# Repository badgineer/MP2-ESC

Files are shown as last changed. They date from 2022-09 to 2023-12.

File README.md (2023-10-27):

# **MP2_ESC** 
Multi-Platform, Modular, Powerful Electronic Speed Control

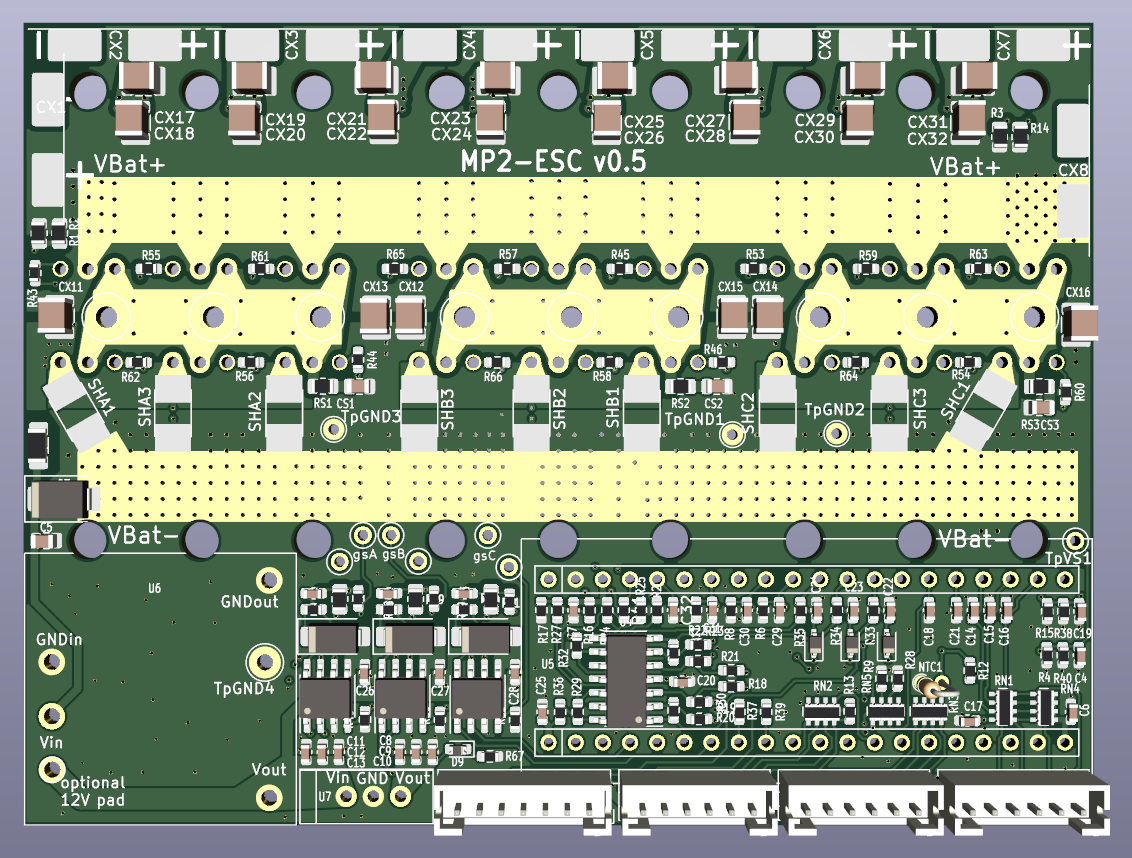
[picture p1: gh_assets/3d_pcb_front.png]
3D_PCB


## Design Goals
**Decent power** (18 FET, so 100-300A should be possible depeding of FET choice, Bus Bars, and cooling) \
**Relatively compact design**, fitting for ebikes / medium-large electric scooters, and cheap to order \
**Modular**, with easily replaceable modules (both bluepill and blackpill compatible hardware wise, 12V and 5V DC-DC stages are modules also) \
**Standard footprint parts**, so replacement parts can be found easily in case of original parts out of stock or out of production \
**Optimized for low cost** production by JLCPCB, including SMT assembly.  \
**Possibility to buy the SMD parts pre-soldered:** All SMDs are on the same side, in large stock at lcsc (at the time of writing), so the board can be ordered with SMDs pre-assembled by JLCPCB for a decent price. \
**To our knowledge, important feature that is not available on most open source ESCs:**
* hardware overcurrent proection (triggers at 430A)

## Compatibility with variaty of Open-Source VESC projects
VESC with [ STM32F405 pill ](https://github.com/davidmolony/F405_pill)  \
VESC with GD32F303CG pill (Netzpfuscher mod, note CG) \
EBICS with F103 Bluepill (Stancecoke) \
[SmartESC V3 (Casainho)](https://github.com/casainho/SmartESC_STM32_v3) \
[SmartESC V2 (Netzpfuscher/Koxx3)](https://github.com/Koxx3/SmartESC_STM32_v2) \
MESC with F401 Blackpill (MxlemmingFOC) \
STM32 Motor Control Workbench (F401, F103)

## PCB
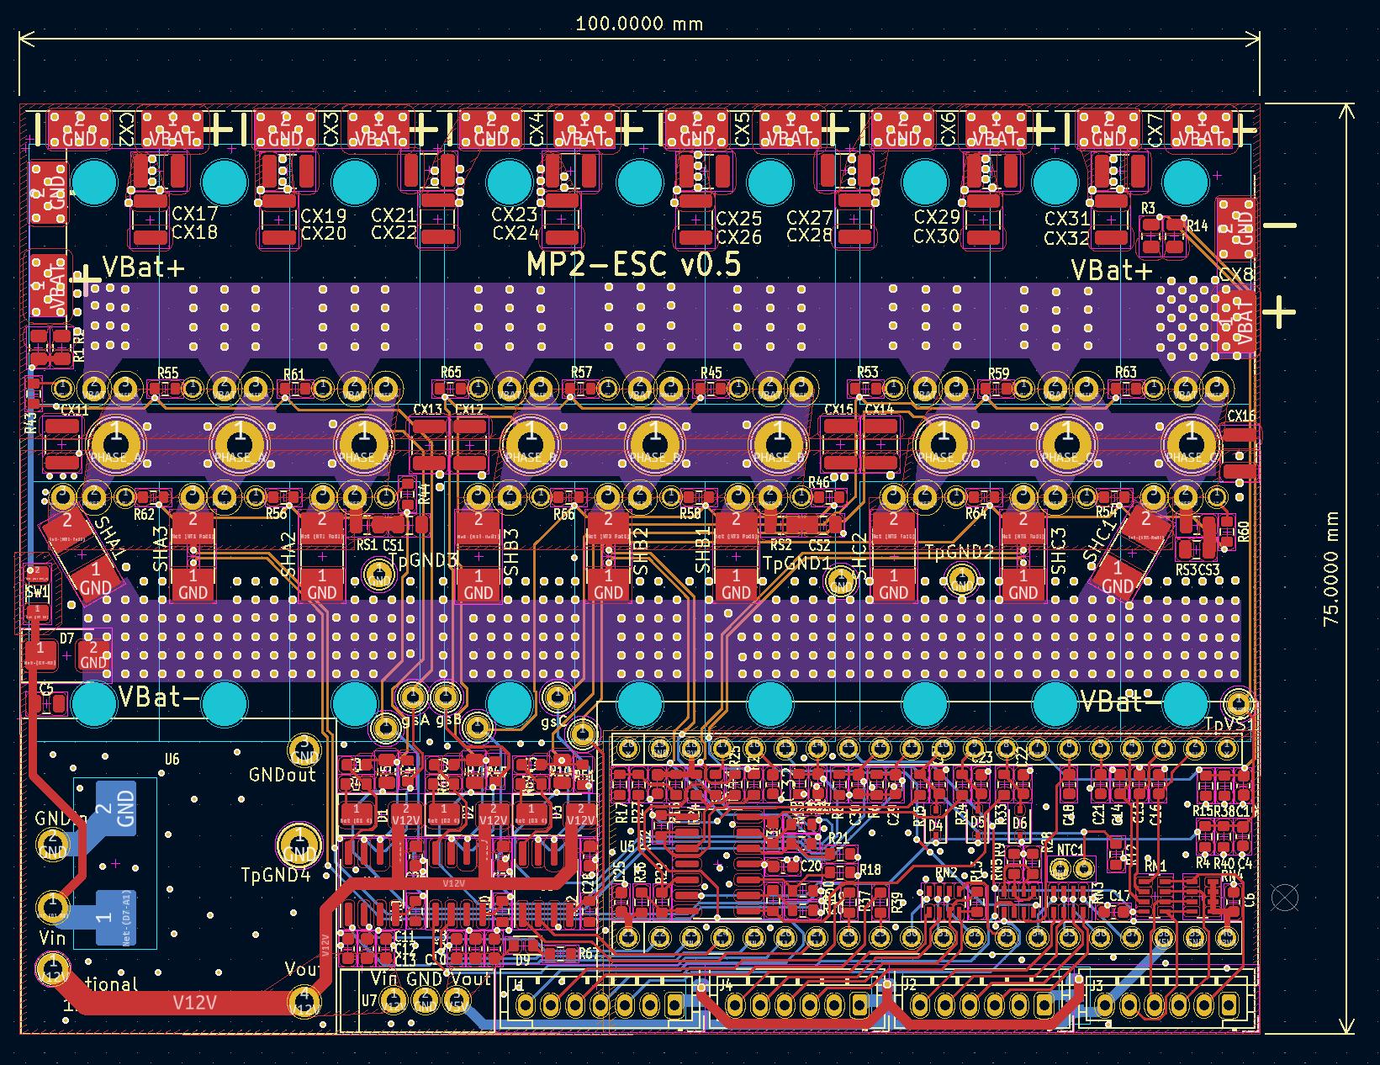
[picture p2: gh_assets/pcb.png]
PCB


## Required software
The circuit design tool used for this project: [KiCad](https://www.kicad.org/).

## Endless Sphere Thread:
https://endless-sphere.com/forums/viewtopic.php?t=117045

## Safety
The high amperage and compact design of this board means that it is inherently prone to arcing. For this reason we urge you to engage in the following safety precautions:

* Remove all sources of power when operating on the board. This includes soldering, mounting the board, connecting wires, or plugging in the pill
* Use an [USB isolator](https://www.amazon.com/s?k=usb+isolator) when connecting to your computer
* **DO NOT USE LIPO BATTERIES INDOORS**
* The board stores considerable capacitance -- a spark when you connect to your power supply
* Ideally you should use a current limited power supply when testing
* Before powering up **follow all recommendations in our building tips section**.

## Building Tips

Soldering, assembly, safety and testing are [here](docs/PCB_ASSEMBLY_TESTING.md).

### **Bus Bars**
Bus bars are recommended for anything else than very low current. (extra copper wires/bars/plates soldered to the exposed copper strips of the PCB, or at very least a ton of solder on the exposed strips, but this last variant only for low phase currents). See [this document](docs/HIGHER_AMP_ASSEMBLY.md) for examples. 

### **Bulk electrolytic capacitors (XC.... )**
We recommend a total of 2000uF for low phase currents (up to ~150A) and 3000uF or more for high battery currents. There are 2 smt pads at the ends of the Vbat bus bar, and another 6 on the top for usecases where a lot of capacitance is needed.
General considerations: You need more capacitance the more phase current you plan to use, and the longer (and thinner) your battery wires are. So you can probably also get away with less if you have short thick battery wires.  

Choose voltage rating ~ 1.5x your max battery voltage for a long lifetime. For 48v nominal (54.6V max) battery voltage, 80V or more is recommended. Or just use the same rating as your FETs.  
The total capacitance of the electrolytic capacitors is more important than the exact combination of values. More smaller capacitors probably have a slight advantage over fewer large ones: lower ESR, lower parasitic inductance, and redundancy in case of failures.

### **Bulk ceramic/MLC capacitors:  (XC.... )**
As much as possible. These need to compensate for the high frequency weakness of the electrolytic capacitors. Overrating voltage rating is recommended. 

### **Capacitors - the rest**
Values are consolidated for easy buying. Voltage rating is 25V or higher regardless if they are on the 12v, 5v, or 3v3 rail on the default design, however you can choose a smaller voltage rating for the 5v and 3v3 rails..  

### **Snubbers (RSx, CSx)**
These are RC snubbers. **They are here only for the footprints. Do not fit them (yet).** The real values (if necessary at all) will be computed after we build the controller and see what ringing we get. Purpose of the snubbers is to dampen that ringing. (if you choose different parts than the one we compute the snubbers for, you might need to compute the snubbers yourself). These components are not present in the pick-and-place or BOM files.

### **MOSFETs**
The default MOSFETs are available from lcsc at the time of writing. They are cheap and have good specs. (low Rds on, low Crss, 100v, etc). 
You can use a FET of your choosing, but please be aware that old FETS (such as the famous 4110 or 3077) have huge Crss, leading to a tiny Ciss/Crss ratio. This ratio needs to be bigger than roughly your max battery voltage, so you will need to compute and add the optional Cgs capacitors (OCx). Small Ciss/Crss results in ringing / parastic turn on (which leads to failure). 
That being said, it’s best to just use FETs with Ciss/Crss > ~100, nowadays they’re easy to find. See the section with alternative parts below.

Some additional material on MOSFET selection and testing is [here](docs/MOSFET_PARAMETERS.md).

Attach the FETs to a heatsink: the FETs need to be electrically isolated from the heatsink, but well connected thermally. The options for this are:
* Mica glass (“traditional option”, cheap, easy to find)
* Ceramics (saw this as a new option, never tried it)
* Polymer pads 
* Kapton Tape 

Unfortunately in focusing on making the board small we crammed the FETs very close together. This means some mica or ceramic pads will not fit - and it’s very hard to cut them afaik. So for this version we’re probably stuck with polymer / kapton. 

### **Board Testing**

* V0.1 build has been tested by mxlemming with MESC FOC firmware on F401CC black pill board, and by Netzpfuscher with his VESC port, in lab conditions. 
* V0.3 has been tested, and reached 280Phase amps on a Surron, with maximum power draw 10kW. There were no overheating problems (though cooling was good, and it was winter). Over 280 Phase amps there were random BRK errors (a fix is being tested)

### **Known issues/limitations:**
* Pills have very few ADCs, so some sacrifices have been made (choice between analog brake and Motor Temp). 
* Gate drivers are not as popular and readily available on lcsc as the other SMD parts
* Having the MCU on a separate board (the "pill" development boards) is a questionable idea from PCB design point of view. In our testing it seemed to work, but we know it's not without drawbacks (main one being pill pins "catch" noise).

## Alternative parts.

### **MOSFETs**
100V: 
* CRST030N10N - Default, cheap, tested, available at lcsc.
* MDP10N027 - Cheap, tested, available on aliexpress.
* IPP023N10N5 - Good, more expensive, not tested.

80V: 
* CRST030N10N - Very cheap, not tested, lcsc.
* IPP019N08NF2S - Good, more expensive, not tested
* IPP016N08NF2S - Very good, more expensive, not tested

150V:
* CRST073N15N
* NCEP15T14
* NTP5D0N15MC - best of the 3 listed here, not tested. 

Generally: There are a lot of TO220 fets to choose from (probably the only real advantage of TO220). If you want another, make sure it has low RDSon, gate charge ~ 160nC, low Crss (Ciss/Crss > Vbat).  

### **Gate Drivers**
* L6498DTR - ST micro. default. not tested yet
* EG2181D - EG micro. not tested, cheap on lcsc
* TF2190M-TAH (TFSS) (LCSC PN: C2917161) -> tested. probably has problems with ulvo, which result in shoot through. not recommended anymore (used to be the default.)
* NCP5183/NCV5183 (On Semi)
* FAN7390 (Fairchild)
* FAN7191 (Fairchild)
* DGD2190M (Diodes Inc)
or any other "replica" of IR2181

### **Operational Amplifier**
* NCS20034 (On Semi) - tested
* GS8634-SR (Gainsil)
* COS724SR (Cosine) - tested. current default recomendation due to specs and LCSC stock
* TSV914 (ST)
* TLV9054 (TI)

### **Pills**
* F405 Pill - [ LINK ](https://github.com/davidmolony/F405_pill) 
* Black Pill
* Blue Pill

### **12V DCDC**
* We recommend isolated:
  * PQDE6W-Q110-S12-D preferred (CUI devices)
  * RD5-110S12W (Rui Da Kang)
  * HLK-10D11012 (HiLink)
  * RDE20110S12 (XP Power)
  * THN 10-7212WIR (TRACO Power)
* Less desireable: unisolated
  * P7805-500 (CUI)
  * Or wire on some [random cheap stuff](https://www.aliexpress.com/item/1005001599313771.html)

### **5V DCDC**
* Tons of options in "TO220 Replacement" format - like [ this random example ](https://www.aliexpress.com/item/1005004807082011.html)
* VXO7805-500 (CUI)
* VX7805-500
* 7805SR-C (Murata)

### **Diodes for "over" protection**
1N5819WS - These are ubiquitous, but it is important you use these due to very low forward voltage. Using anything else will probably result in hardware overcurrent not working.

### **Diodes for bootstrap**
We recently changed from XX4007 in SOD123 package to higher speed diode (US1M). Anything with 100V+ or 150V+ will work... but generally many 1kV diodes are available in common packages, so use them. High speed are preferable, but really most diodes will work...

## Supporting materials
* Gathering motor parameters [[LINK](docs/MOTOR_PARAM.md)]
* MOSFET selection [[LINK](docs/MOSFET_PARAMETERS.md)]
* Pin mappings between MP2 and the F405 pill [[LINK](docs/MP2_F405PILL_PINOUTS.md)]
* MP2 assembly, testing and firmware [[LINK](docs/PCB_ASSEMBLY_TESTING.md)]
* MP2 bus bar methods [[LINK](docs/HIGHER_AMP_ASSEMBLY.md)]
* MESC Firmware on the MP2 -- getting started with STM32CubeIDE [[LINK](docs/FIRMWARE_INTRO.md)]
* Some (bad) examples of connecting the MP2 to a motor [[LINK](docs/QS165_MP2_WIRING.md)]

## Change Log / Known Problems 

### v0.6 change log
* R17 of the opamp comparator changed to 22k -> back to actual 430A overcurrent protection, was 375 out of an error
* removed vsense 2 - hardware overvoltage also limits battery choice, and is of limited usefulness
* changed default bom to accomodate 32s max battery without modifications. See most below changes. 
* changed all ceramic caps on vbat to 250v rated ones
* removed TVS diodes - they only work for a very low voltage interval, so without its more generic
* changed vbat divider network so it's exaclty the same ratio as phase vsense to make it easy to set up the software (just set 150 and 3.3 everywhere) 

### v0.5 change log
* added bootstrap resistors to limit current spikes
* reduced gate pulldowns to 10k for faster fet turnoff in some cases
* changed the default gate driver (old one was suspected of bad behaviour)
* 1 gate resistor per fet now.

### V0.4 known problems
* bluepill is mostly supported - but due to a pinout bug does not have a cap on RST. Take care if you use bluepill! 
* v0.4 not tested at this time. if you do test it, please let us know. 
  
### V0.4 change log. 
* remove vbat solder jumpers. for 150v the board requires a different BOM anyway.
* remove pill solder jumpers. (bluepill compatibility is a bit complicated because of a pinout mistake)
* make overlimit opamp output LPF better suited to an additional LPF on the pill and reducing pin noise. (cap -> 10uF, move it near pin, decrease R value)
* make power switch footprint more accessible, and less arc prone. (bigger, better location)
* move the protective R pair near vbat ("before" the switch)
* increase margins for Vbat and Phase copper areas to reduce short / arc risk
* replace the 4pin JST with a 7pin one and route more of the pill pins to JSTs
* standardize JST pin layout (GND and Vaux are all over the place.)
* add a power led on 5v rai
* added lpf caps on ADC throttle/brake inputs
* made 12v surface routed 
* phase wire pads are now at equal distance from eachother
* adapted to newest F405 pill pinout 
* moved to kicad 7

### V0.3 change log
* reduced shunt value to 0.5mR (from 1mR) for lower heat generation
* increased opamp gain to ~22 (from 10) for compensating lower shunt value
* added solder jumpers for configuring power stage vsense
* faster/better bootstrap diodes for better behavior and lower Qrr loss/heat
* many other tiny changes / improvements

## FAQ

* **What’s with the many solder jumpers?**
Except for the hall sensor JST, all others have a solder jumper for connecting its power pin to 3v3 or 5v, depending on your needs. 

* **Why do the electrolytic caps have surface pads instead of through hole?**
Through hole pads imply a lead through the hole, sticking out on the other side. This would prevent the FETs from sitting flush against the PCB.

* **Can you assemble it for me?**
There is no plan on selling any assembled PCBs. You can get the SMD side pre-assembled at [jlcpcb](https://jlcpcb.com/) (at the time of design all parts were in stock for jlcpcb SMT service). So you’ll only need to solder the through-hole parts and the modules. 

* **I want more power!!!**
This might not go well. So good luck, you’ll probably need it. Please don't blame us when it goes up in smoke. But do let us know how it goes. Disclamer aside, here are some basic suggestions:
   * Review what [other people](docs/HIGHER_AMP_ASSEMBLY.md) have done.
   * Add thick copper bus bars to the board.
   * Add more/ bigger bulk caps!
   * Use appropriate wires (thick!) 
   * Overcurrent trips at 430A. If you want to come close to it / exceed it, either cut off  the overcurrent circuit by desoldering D4, D5, D6, or be creative with the shunts. But 150A per TO220 fet is a crazy idea.

* **I want more voltage!!!!**
Realistic limit is 30s lipo for 150V rated components. For more than that the ESC will need serious redesign. 

* **Your part X is bad, I recommend Y!**
We tried to find cheap but decent parts for this controller. Cheap almost always implies a compromise in some other areas, so you might not like our pick :)
It should be fairly easy to switch to other parts on your own: we used mostly standard and popular footprints and packages
If you know better parts or have better solutions, please let us know on our ES thread. We like learning new things. 
....except if you’re going to suggest 3077 or 4110 mosfets. Those things are dinosaurs. They were the biggest baddest thing around during their time, but nowadays belong in a museum. Or on a t-shirt. Please stop recommending them. 

* **Where can I buy parts?**
Lcsc.com, mouser.com. Aliexpress if needed. 
We designed this with jlcpcb smt assembly in mind, so all SMDs were in stock at lcsc when I designed the PCB. Also most of the Through-hole parts. 

* **This whole thing is amateur work!**
Yeah, totally true. We are mostly amateurs working on a generic ESC for free. If by this you refer to any specific mistake / set of mistakes, we would love to know about it! Post in the ES thread. Thanks!

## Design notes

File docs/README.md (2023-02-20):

# Documentation for MP2

**The documentation that we have here attempts to help people at many different skill levels to better understand the MP2, as as other Electronic Speed Controllers (ESCs). What is important is that the MP2 is not a commercial ESC. It is not possible to contstruct, test and run MP2 without a basic understanding in electronics, circuit construction, C-programming and the general principles behind BrushLess DC (BLDC) motors. We have a partial collection of materials to help, and we're also going to assume when it comes to something like running an oscilloscope you can search the web to educate yourself. Good luck.**

The following are some resources that we strongly encourage you to read and understand before proceeding:
## Appnotes ##

A couple of appnotes that walk through BLDC operation [[LINK](https://www.monolithicpower.com/media/document/Brushless_DC_Motor_Fundamentals.pdf), [LINK](https://www.monolithicpower.com/media/document/Brushless_DC_Motor_Fundamentals.pdf), and [LINK](https://www.st.com/resource/en/application_note/cd00020086-sensorless-bldc-motor-control-and-bemf-sampling-methods-with--st7mc-stmicroelectronics.pdf)]. In addition to explaining a lot of the general principles of BLDC operation, these texts will help you start to get familiar with a lot of important terms involved with motors. 

## Youtube videos

* An in depth introduction to ebike motors and controllers [[LINK](https://www.youtube.com/watch?v=c96n0Ma2rLY)]
* A deeper dive by into motor considerations from the same presenter [[LINK](https://www.youtube.com/watch?v=dxJe_gygRGU)]
* How PWM signals are generated to create sinusoidal commutation [[LINK](https://www.youtube.com/watch?v=-By_vt27Xhs)]
* (I'd be curious to know if the MESC uses the state space vector approach here: [[LINK](https://youtu.be/-By_vt27Xhs?t=164)]
* A very nice series relating motor behavior important math principles [[LINK](https://www.youtube.com/watch?v=EHYEQM1sA3o)]

## MP2 Operations

Readers are also strongly encouraged to read documentation [[for the MP2](https://davidmolony.github.io/MESC_Firmware/)]. 

And our own David Molony has created several instructional videos for the MP2
* [STUB] Be sure to have a look at this flow diagram depicting fast and hyper loops, and these two videos
* [LINK](https://youtu.be/D8OxaPtngFE) Description.
* [LINK](https://youtube.com/shorts/5mvyW02K6BA) Description.
* [LINK](https://youtube.com/shorts/p_EUAOHa-1w) Description.
* [LINK](https://youtu.be/9agJsvzlajI) Description.
* [LINK](https://youtube.com/shorts/ht_xRyyBOWQ) Description.

## Flashing, MP2 assembly, and construction
* MESC Firmware on the MP2 -- getting started with STM32CubeIDE [[LINK](FIRMWARE_INTRO.md)]
* Gathering motor parameters [[LINK](MOTOR_PARAM.md)]
* Pin mappings between MP2 and the F405 pill [[LINK](MP2_F405PILL_PINOUTS.md)]
* MP2 assembly, testing and firmware [[LINK](PCB_ASSEMBLY_TESTING.md)]
* MP2 bus bar methods [[LINK](HIGHER_AMP_ASSEMBLY.md)]
* Some (bad) examples of connecting the MP2 to a motor [[LINK](QS165_MP2_WIRING.md)]
* Gallery of enclosures [[LINK](ENCLOSURE_GALLERY.md)]

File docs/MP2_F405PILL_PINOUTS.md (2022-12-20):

# MP2 V0.3 JST PINOUTS

## Translation table for VESC users

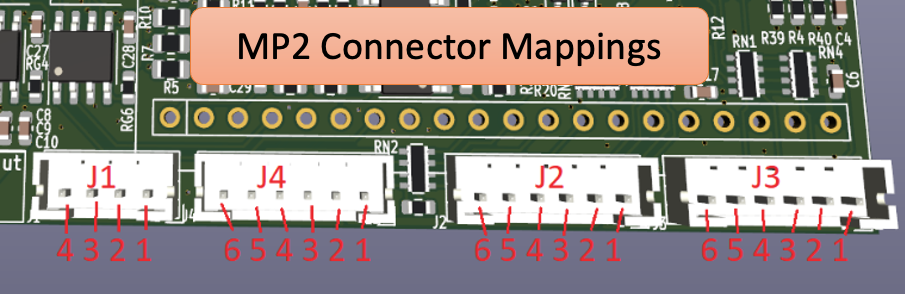
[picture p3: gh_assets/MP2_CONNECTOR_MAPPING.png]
Pins to MP2 Function of MP2 pins


| |VESC F405 Pill| |
|:----|:----|:----|
|Header|MCU pin|Name|
|J3 - 1|N/A|GND|
|J3 - 2|PC8|HALL_A|
|J3 - 3|PC7|HALL_B|
|J3 - 4|PC6|HALL_C|
|J3 - 5|PA7 (opt)|MOTOR_TEMP|
|J3 - 6|N/A|5V5|
| | | |
|J2 - 1|N/A|Vaux (5v or 3v3)|
|J2 - 2|N/A|GND|
|J2 - 3|PB9|CAN_TX|
|J2 - 4|PB8|CAN_RX|
|J2 - 5|PB11|USART3_RX|
|J2 - 6|PB10|USART3_TX|
| | | |
|J4 - 1|N/A|GND|
|J4 - 2|N/A|Vaux|
|J4 - 3|PB4|TIM3 / MISO|
|J4 - 4|PB5|TIM3 / MOSI / CAN2_RX|
|J4 - 5|PB6|TIM4 / CAN2_TX / USART1_TX|
|J4 - 6|PB7|TIM4 / USART1_RX|
| | | |
|J1 - 1|N/A|GND|
|J1 - 2|PA4|A_THROTTLE|
|J1 - 3|PA7 (opt)|A_BRAKE|
|J1 - 4|N/A|5V|

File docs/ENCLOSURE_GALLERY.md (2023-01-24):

# MP2 Enclosure Gallery

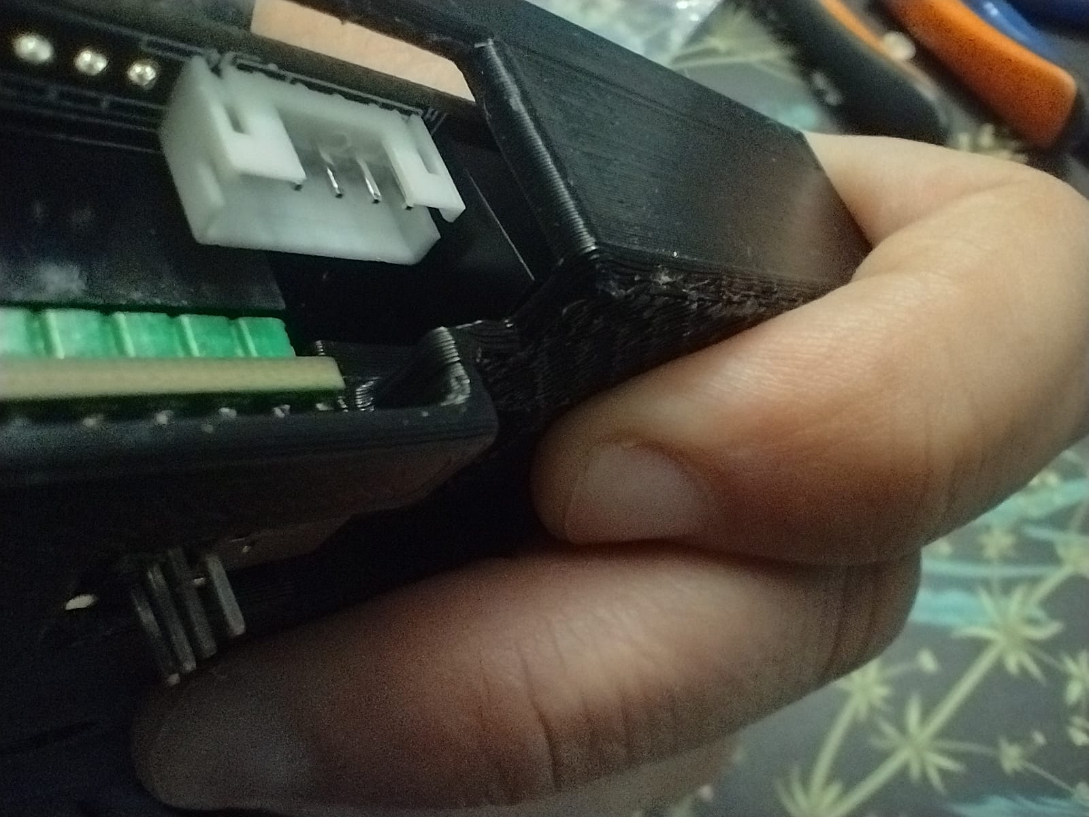
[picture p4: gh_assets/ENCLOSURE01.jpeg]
example1

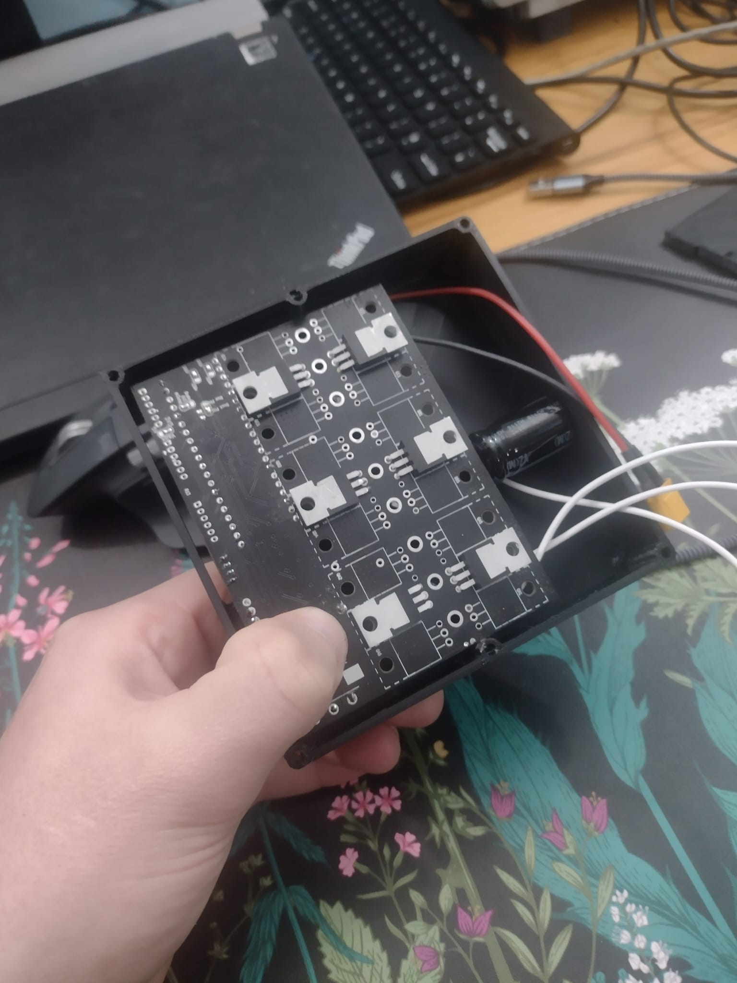
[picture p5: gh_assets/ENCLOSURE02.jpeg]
example2

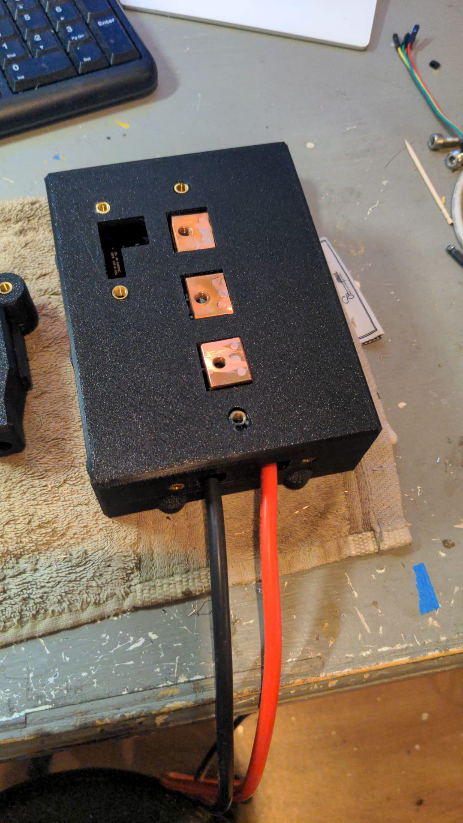
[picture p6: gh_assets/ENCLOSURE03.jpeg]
example3

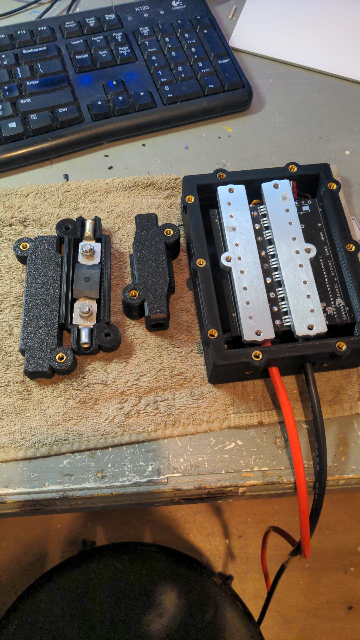
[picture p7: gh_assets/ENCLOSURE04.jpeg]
example4


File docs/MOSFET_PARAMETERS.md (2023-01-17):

# Choosing MOSFETs for the MP2 Controller

## Relevant MOSFET Specifications
Drain-source Breakdown Voltage (BVdss) refers to the voltage across the drain-source terminal that causes the drain current (ID) to suddenly rise. Drain-source on-resistance (RDS(on)) refers to the effective resistance between the drain and the source when the MOSFET is in the on state. RDS(on) impacts the max current rating of the MOSFET and the heat generated by the MOSFET is directly proportional to this value. RDS(on) is also associated with current loss. So when choosing a TO220 MOSFET package for the MP2, follow these values closely. 

For MOSFETs on the MP2, you want:

BVdss = 20% margin over your battery’s max voltage 
RDS(on) <= 4mOhm 

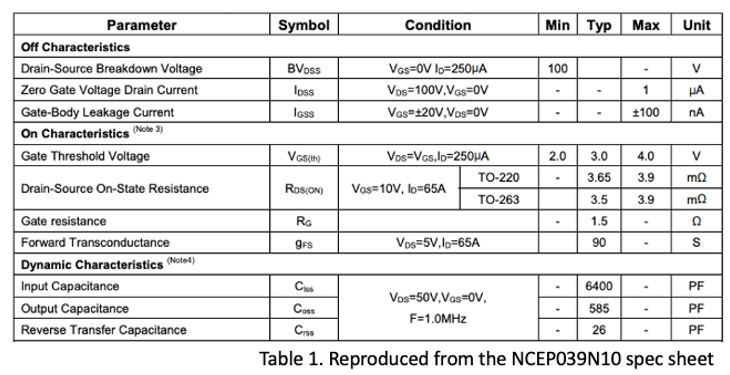
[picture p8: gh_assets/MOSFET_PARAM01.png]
Table 1


## Avoiding Parasitic Activation 
The gate of a MOSFET is insulated by a thin silicon oxide which results in a capacitance between the gate-drain, gate-source and drain-source terminals. The capacitance values are described by the Input Capacitance (Ciss) and  Reverse transfer capacitance (Crss) directly reflect the switching performance of a MOSFET. (Other factors like reverse recovery charge can also be considered). These Ciss/Crss capacitances form a potential divider between the battery and the MOSFET source. Much like resistors, they have the effect of pulling the gate up or down when the MOSFET switches. Figure 1 shows that when the gate voltage bumps above the threshold, current starts to flow and it short circuits the battery. This is a problem. Quoting [this document](https://drive.google.com/file/d/1NGAKFHYZfCwJLpQ9wMGC9iVUuzCymuSV/view), “parasitic, or unwanted, turn-on of the power MOSFET is a phenomenon which happens in the reality more often and can cause more damage then usually known. Its appearance often leads to the destruction of the MOSFET…”. To avoid unusual destruction from parasitic turn on, select a MOSFET with a high Ciss/Crss ratio. You are looking for something like what is shown in Table 1 -- as long as that data is true -- we have a ratio of ~200, and the MOSFET should be immune to parasitic turn-on. 

Another consideration is the Gate Threshold Voltage (Vgs) which characterizes the voltage between the gate and source that will switch on the MOSFET. When Vgs is exceeded, the MOSFET turns on and Drain Current (e.g., "ID") begins to flow. The Transfer Characteristics of a MOSFET shown in Figure 1, displays a knee in the curve around 4V which is good because at this level the MOSFET is more resistant to parasitic turn on.  But be careful -- a higher Vgs is usually at the expense of some RDS(on) -- which we want to minimize. 

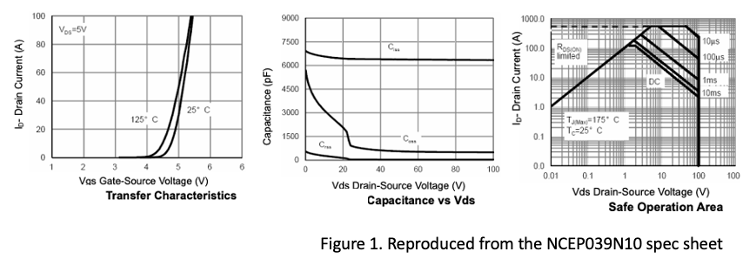
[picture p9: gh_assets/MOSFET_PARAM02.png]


## Optimum Dead Time Values
The MP2 uses a half bridge configuration shown in Figure 2 with two N-channel MOSFETs between Vbat and ground to drive each motor phase. The two half bridge MOSFETs are referred to as “high-side” and “low-side”. During its operation the high-side and low-side MOSFETs trade switching between each other in order to drive current to each motor phase. Shoot through refers to a situation where both high-side and low-side MOSFETs are simultaneously fully or partially turned on, allowing current to flow between Vbat to ground. Dead time, refers to the period of time between switching the MOSFETs to protect against shoot through. 

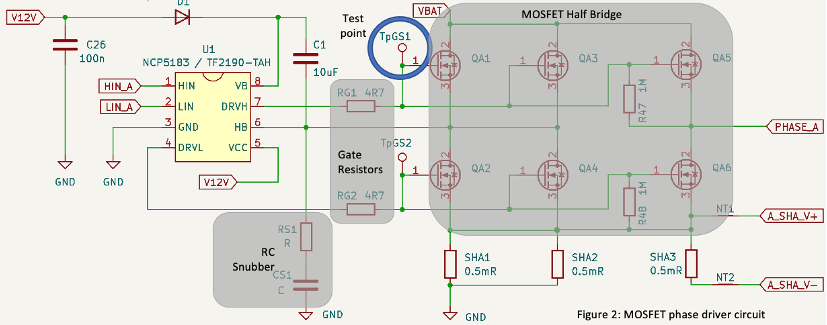
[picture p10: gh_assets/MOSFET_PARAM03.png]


Factors that control how quickly MOSFET switching also important to setting the correct dead-time. For example, depending on the selection of the parts you’re using, the MP2 may have 4.7 ohm gate resistor with 3 x 7.4nF capacitance. This combination of factors gives a time constant of 104ns. Turn on threshold is usually reached within 1 time constant and turn off in 1.5 to 2.5 time constant. MP2 users will therefore need at minimum 1 time constant dead time to avoid the high and low side MOSFETs coming on at the same time. There is additional resistance coming from the MOSFET driver which impacts switching, and the capacitance between the drain and gate (i.e., "Miller capacitance") also reduces the switching speed.  Rise time for the MOSFET is also associated with Ciss as well as the package temperature. Taken all together, in practice, 3 time constants dead time is minimum, 4 usually optimal, and 5 is safe.

## Snubber Resistors
Surges of voltage between the MOSFET drain and source are able to feed back through the gate because of electromagnetic induction and parasitic capacitance resulting in unwanted oscillation, which is often referred to as "ringing".  These transient voltages are shown in Figure 3. Ringing is inevitable with fast switching, but snubbers in the circuit reduce the overall gain of oscillation and will decay the oscillation more rapidly. Depending on the choice of MOSFET you select, the MP2 may not need snubbers, but as you can see in the [MP2 schematic](https://drive.google.com/file/d/1S_ANmKU4OLiC335F1DV1td9k-rrzCTln/view) it is equipped with snubber resistors (RS1, RS2, RS3) and capacitors (CS1, CS2, CS3). 

In situations where you get ringing on the MP2, you will need to dampen the oscillation by choosing the R and C snubber values, and soldering in these components. (Dont panic, the footprints for these components are 2.0 x 1.2 mm.) Look at the behavior of the MOSFETs on the MP2 by running it at moderately high current, and putting an oscilloscope probe on the test points connected to the MOSFET gates. (The test points are labeled with “TpGS” on the schematic.) The ringing frequency will be in the 20 to 150MHz region. You then tune the snubber so that it dampens the targeted ringing frequency. To achieve this, set C to roughly half the MOSFET total Coss (output capacitance) and the R such that the RC frequency is equal to the ringing frequency. If that doesn't solve ringing problems, you may have to increase the gate resistors (labeled RG1-6 on the schematic) which currently are 4.7 ohm. Changing these resistors may also require modifying the dead time. 

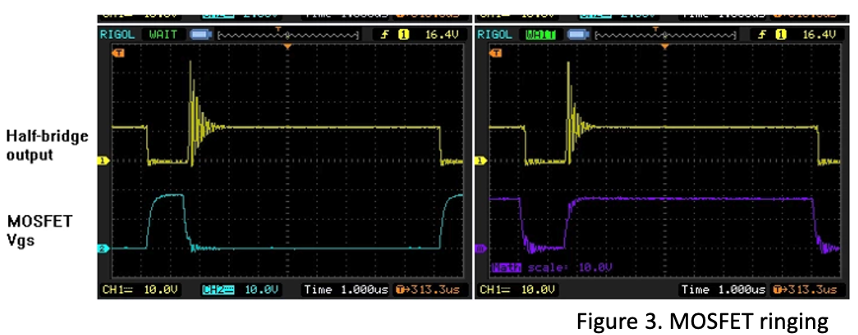
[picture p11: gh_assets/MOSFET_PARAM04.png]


A practical example (text taken from the [MP2 schematic](https://drive.google.com/file/d/1S_ANmKU4OLiC335F1DV1td9k-rrzCTln/view))
Rough approximation: RC = 1/2 ringing period, e.g. 30MHz ringing -> 3ns period ->1.5ns RC, 2nF 1ohm is a good starting point. Typically, C = 1-5nF, R = 0.5-5 ohms. The capacitor determines the power dissipated, the resistor dissipates the power. The highest damping factor usually where Csnub ~=Coss MOS.

Other MOSFET Properties: Switching Losses
Earlier we said RDS(on) is associated with the MOSFET’s current loss, which translates to a power loss in heat which can be described by this equation:

P=(√2xI)² x RDS(on)

Where I represents currents and the units for P is in watts. This is time shared between high and low side so a further division by 2 is required.

Switching losses are described by:
 
Vbus x Iphase x switching time.
 
Where Iphase is average (not RMS) and switching time will be measured using a scope. Body diode conduction losses are given by:

Dead time x Iphase(avg) x Vdiode x Fpwm x 2 

Where dead time is the effective dead time where both MOSFETs are actually off, ~200ns if set up well, Vdiode is usually 1volt, Fpwm x 2 is per phase. 

Note, loss to the gate resistors is negligible and overall, RDS(on) usually dominates switching losses. 

## Suggested MOSFET Part Numbers (from [Endless sphere](https://endless-sphere.com/forums/viewtopic.php?t=117045))

100V
* CRST030N10N (Initial boards built with these)
* MDP10N027 (another initial board built with these)
* NCEP039N10
* IPP026N10NF2S
* DMTH10H005SCT

150V
* CRST073N15N
* NCEP15T14
* NTP5D0N15MC
* SUP70042E

## Issues With NCEP039N10

These MOSFETs have about 2/3 the gate charge of ones previously tested. This may result in ringing problems, and they may have excess dead time that will reduce sensorless startup performance and waste a bit of power.

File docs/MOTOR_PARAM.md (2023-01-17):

# Calculation of BLDC Motor Parameters

The MP2 as well as other VESC-based systems provide the capability to measure motor parameters using the controller. For example, [vesc-tool](https://vesc-project.com/vesc_tool) collects several motor values from a connected motor and controller by selecting "FOC" on left panel, going to the "General" tab, and following the "Detect and Calculate Parameters" directions on that page. 

So vesc-tool is great for retreiving parameters. However, in cases where you want to measure the parameters yourself or check if your VESC is gathering up the right numbers, this document is for you. 

## PREAMBLE
Some notes before beginning.

**Expertise.** This document assumes you have a reasonable understanding of concepts such as Ohm's law and inductance. It also assume that you're comfortable connecting up high amperage equipment which should be not any more complex than wiring your motor to a controller. You're also going to need to have a lot of familiarity with using VESC-based controllers. 

**Equipment.** In order to do what is described here you'll need the following: 
* A multimeter
* A current limiting power supply
* A LCR meter
* An oscilloscope

You'll also need some way to turn your disconnected motor at a relatively precise rpm. More about that later. 

**BLDC motor configuration.** BLDC motors have two basic achitectures:

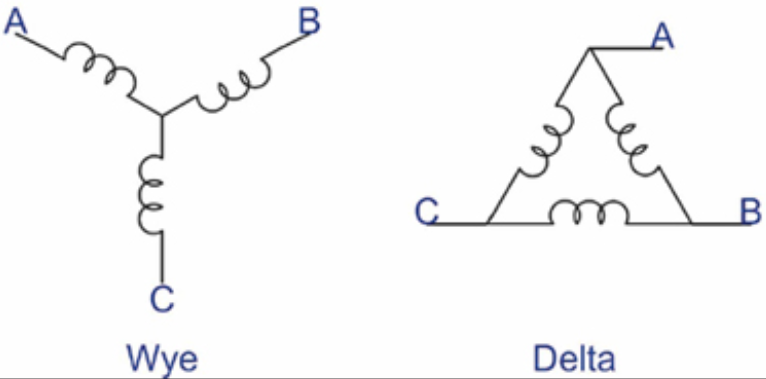
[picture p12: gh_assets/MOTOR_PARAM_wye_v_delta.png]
Figure 1: motor configurations


If your BLDC has three big wires coming out of it, we are going to assume that motor is in Wye configuration for the sake of simplifying the math used here.

## RESISTANCE

The copper wires inside of a BLDC are long, and the resistance found in those windings is an important number. In some cases the resistance can be measure direcly with an ohmmeter, but cheap commerical ohmmeters often will not get down to the range needed to get a good value. Instead, perform the following:

* Find the rated amperage of your motor
* Select a value around 10% of this rating
* Set your current limited power supply to your selected amperage

Your motor has three wires -- these are referred to as "phase wires" and are connected to the the termination points of the windings shown in **Figure 2**. Arbitrarily choose two wires, and connect them to your power supply. Note: the motor will [jump](https://www.youtube.com/watch?v=oRXPFaZ0nJI) and then freeze to a holding position when you connect the power supply.

Now, at the same connection point of each phase wire, connect your multimeter to measure volts (you'll probably need something in the millivolt range). Get a number. Your results may look something like this:

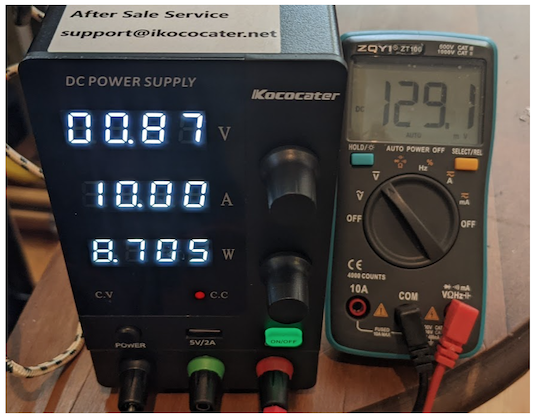
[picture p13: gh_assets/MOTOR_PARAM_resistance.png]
Figure 1. Capturing resistance based on Ohm's law


Notice that it would NOT work well to use the measurement that is coming from the power supply itself. Better to use what your multimeter is telling you. The connection used for this measurement is referred to as "phase to phase" because you're actually connecting between two phases of the motor to get your value. Grab your phase to phase voltage, and use Ohm's law to calculate the resistance. In our case:

* R = V / I
* R = 129 mV / 10A
* R = 12.9
* Convert to single phase resistance: R = 12.9 / 2, or 6.45mOhms

## INDUCTANCE VALUES Lq AND Ld
In our case we're going to measure inductance using an LCR meter. LCR meters measures inductance (L), capacitance (C), and resistance (R) and commercial meters are not particularly expensive.

Gathering inductance values requires that we find two important positions inside of your motor that have to do with the position of the stator coils and the rotor magnets. To find these positions you can use the power supply set at the values as before (or less). These positions are described below:

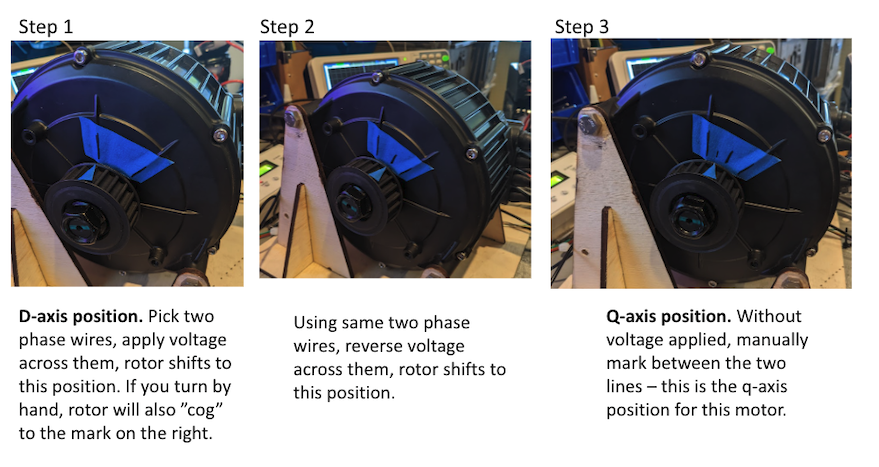
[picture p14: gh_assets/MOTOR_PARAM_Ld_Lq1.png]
Figure 3. D-axis and Q-axis motor positions


Also see [this video](https://youtu.be/oRXPFaZ0nJI) which shows a motor jumping around when the phase wires are connected to a power supply. The marked positions are referred to as d-axis and q-axis (note the above figure). Once you have these positions, do the following:

* Disconnect power supply
* Turn the motor to d-axis position
* Set your LCR to measure inductance
* Using the same phase wires as when connected to the power supply, connect LCR
* Get a reading for Ld
* Turn motor to q-axis position
* Get a reading for Lq

Note, the motor may have residual inductance, or something, that means it takes a while for the L value to settle. In some cases metalic desk tops and placement of hands on the motor have influenced the L value. Take your time, and shorting the leads on the motor also helps to settle residual inductance.

Your measurements for Ld and Lq are phase to phase. Divide by 2 to get single phase Ld and Lq. To get total L for the motor calculate their average, or L = (Ld + Lq) / 2.

In our example here we get the following; (notice the position of the motor in each of the pics):
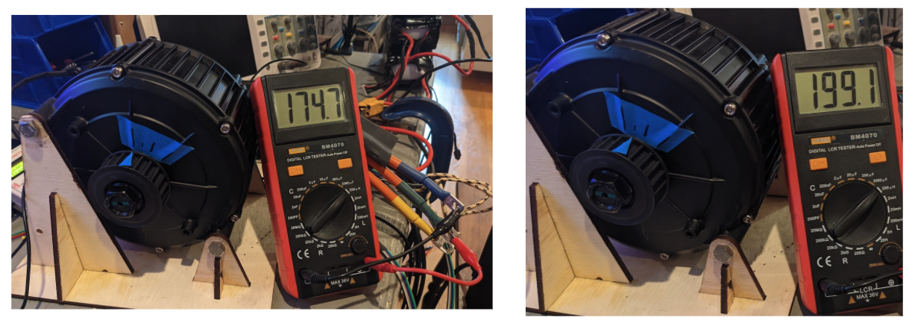
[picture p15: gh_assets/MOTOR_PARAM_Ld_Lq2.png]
Figure 4. Ld/Lq results


* Phase to phase Ld measure = 174 uH
* Phase to phase Lq measure = 199 uH
* Thus, for single phase:  Ld = 87uH, Lq = 99.5uH, and L = 93uH

## FLUX LINKAGE
You'll discover there is an abundance of ways to measure flux linkage out on the internet. In our case we're going to use an oscilloscope to emperically measure amplitude and period of the volts generated by your BLDC. From this we'll calculate lambda, which is the integral of volt x seconds. 

To get this measurement you're going to need some way to turn your disconnected motor at a relatively precise rpm. You'll probably need to mount the motor, and then connect it to an electric drill or another motor. One method of turning a motor is [shown here](https://youtube.com/shorts/YvglKtxUaCQ). Turn the motor and collect the output of the motor on your scope.

Connect the ground end of your oscilloscope to one phase of the motor, and the probe to another phase. Be sure to note the scope settings for volts / div for the amplitude and ms / div for period. Once you have all this extract values for Vpeak and period of your sine wave. Here's an example:

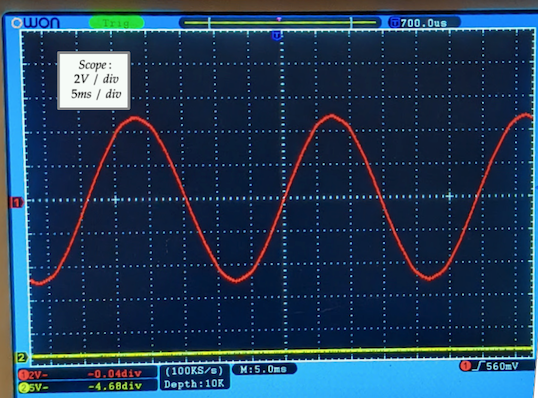
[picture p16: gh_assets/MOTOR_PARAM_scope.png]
Figure 5. Oscilloscope measurements of BLDC motor output


The scope is set to 2V / div for voltage and and 5ms / div for period. In our pic, Vpeak = 5V, and period, or T = 28ms. The formula to calculate lambda is:

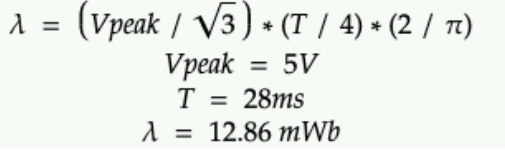
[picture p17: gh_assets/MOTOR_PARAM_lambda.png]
equation for flux linkage


Note: your measurement for the scope is collected from phase to phase; however, this formula does not require that you convert to single phase lambda, the formula handles it for you. 

## COMPARISON TO VESC VALUES

Let's compare these values to what was collected using a 75V 100A single ESC single ubox from Spintend. For the motor used here, this is what you get in vesc-tool by selecting "FOC" on left panel, going to the "General" tab, and following the "Detect and Calculate Parameters" directions on that page:

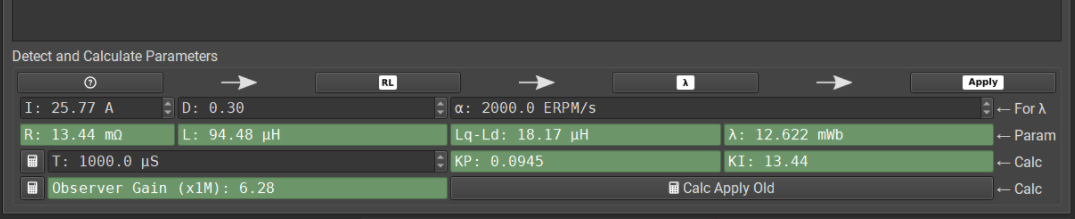
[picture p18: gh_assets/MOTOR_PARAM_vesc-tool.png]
Figure 6. vesc-tool detection results


Comparing to our emperical values, we get:

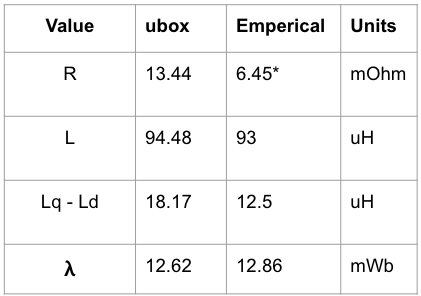
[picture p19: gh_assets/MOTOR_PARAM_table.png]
comparing results


These are values are very close. Note that your results are always going to vary based on your controller, wiring, and motor parameters. 

(*) One exception is the resistance. In this example the resistance of the motor is relatively low and the discrepancy here is probably due to added resistance of the MOSFETs in the ubox. The MOSFET resistance would not be as significant for motors with a higher resistance.

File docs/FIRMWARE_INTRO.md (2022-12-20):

# GETTING STARTED: Install and Debug MESC Firmware

## Getting started
Install STM32CubeIDE from https://www.st.com/en/development-tools/stm32cubeide.html

On the command line clone the github repository using:
```
% git clone https://github.com/davidmolony/MESC_Firmware.git
```

Start up the STM32CubeIDE. A workspace area is used by STM32CubeIDE to store all of your projects. The first time you start STM32CubeIDE it will want to create a workspace, if you dont have one. 

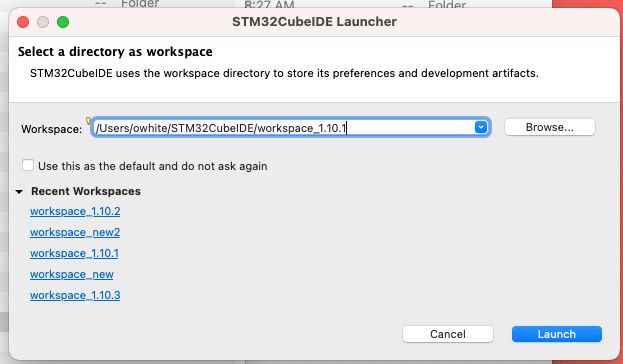
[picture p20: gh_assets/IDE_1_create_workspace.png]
Creating a workspace


Create a name if needed, select "Launch" 

When the IDE comes up for the first time, it may show an information center.

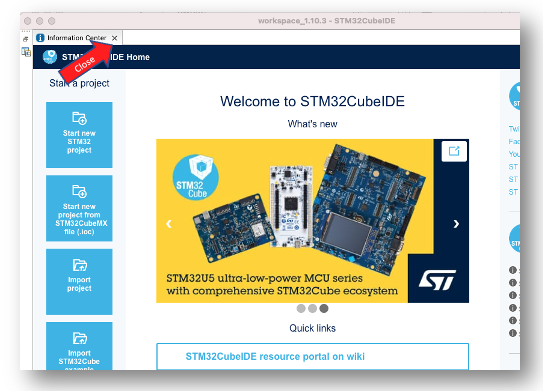
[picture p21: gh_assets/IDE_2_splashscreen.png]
The IDE splash screen


Close on this feature.

The IDE may show a project explorer tab on the left, if you do not see the project explorer:

Window-->Show View-->Project explorer

The project explorer may show "Import projects..." select that, or if you do not see that function, try:

File-->Import...

An import selector should come up:

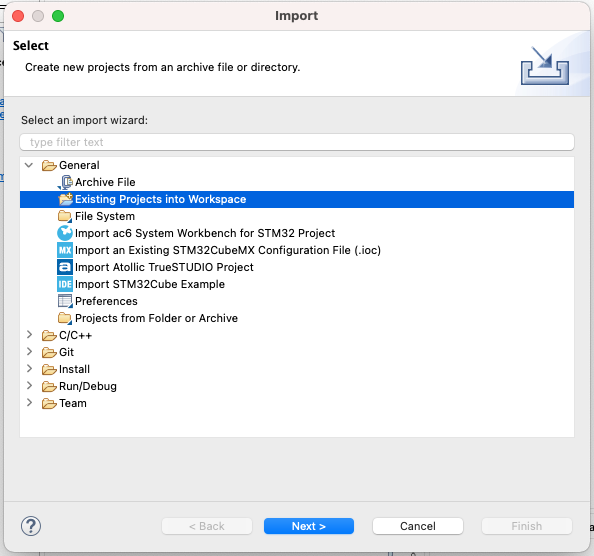
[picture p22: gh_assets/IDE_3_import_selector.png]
Import selection tool


Set up General-->Existing Projects into Workspace, select Next

Browse for the top-level github folder you created, hit open the import function will show this:

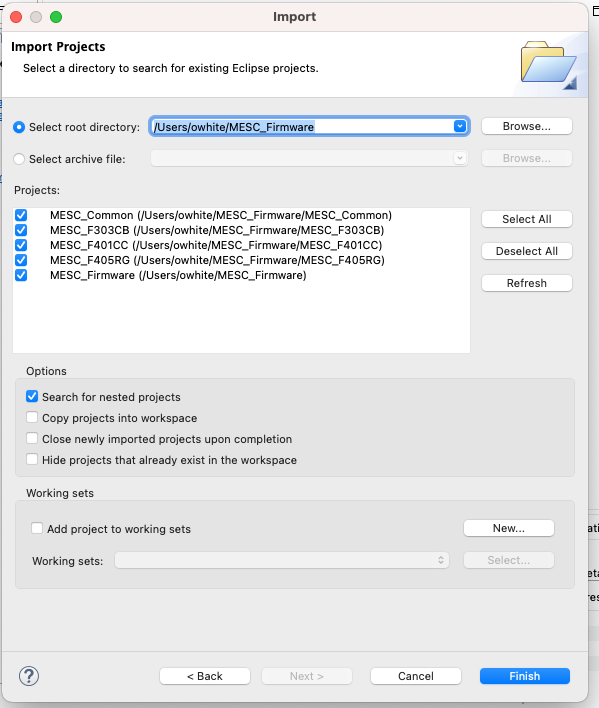
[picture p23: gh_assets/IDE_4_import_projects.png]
Importing projects


Select finish. This should load a set of MESC projects into the Project Explorer, expand the top-level folder and you should see:

At this point if you select

Project-->Build All (or the icons on top of the IDE also help with builds)

you should see the IDE compile the MESC_firmware in all the sub directories. 

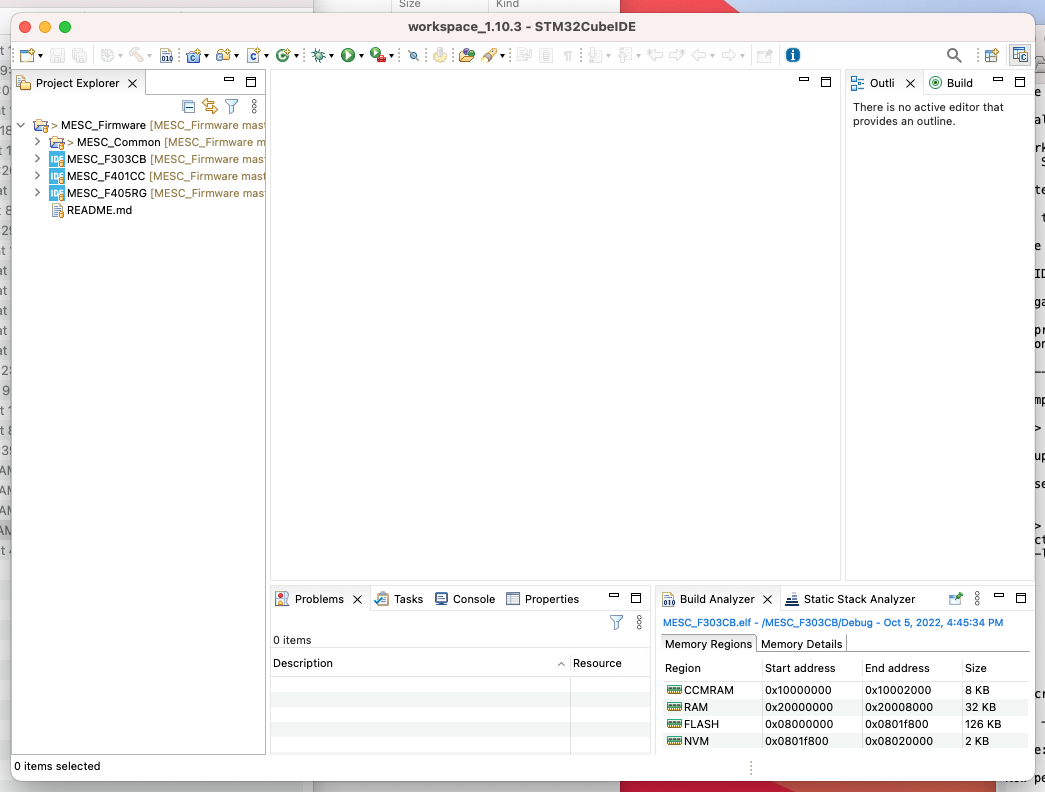
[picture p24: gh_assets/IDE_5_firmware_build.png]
Compiling firmware


When you select the .ioc file in the file browser this tool pops up. By working with the pull down menus on each pin, you can view or set the functions on that pin. This tool also allows you to change many other functions like the timers, UARTS, and ADCs. 

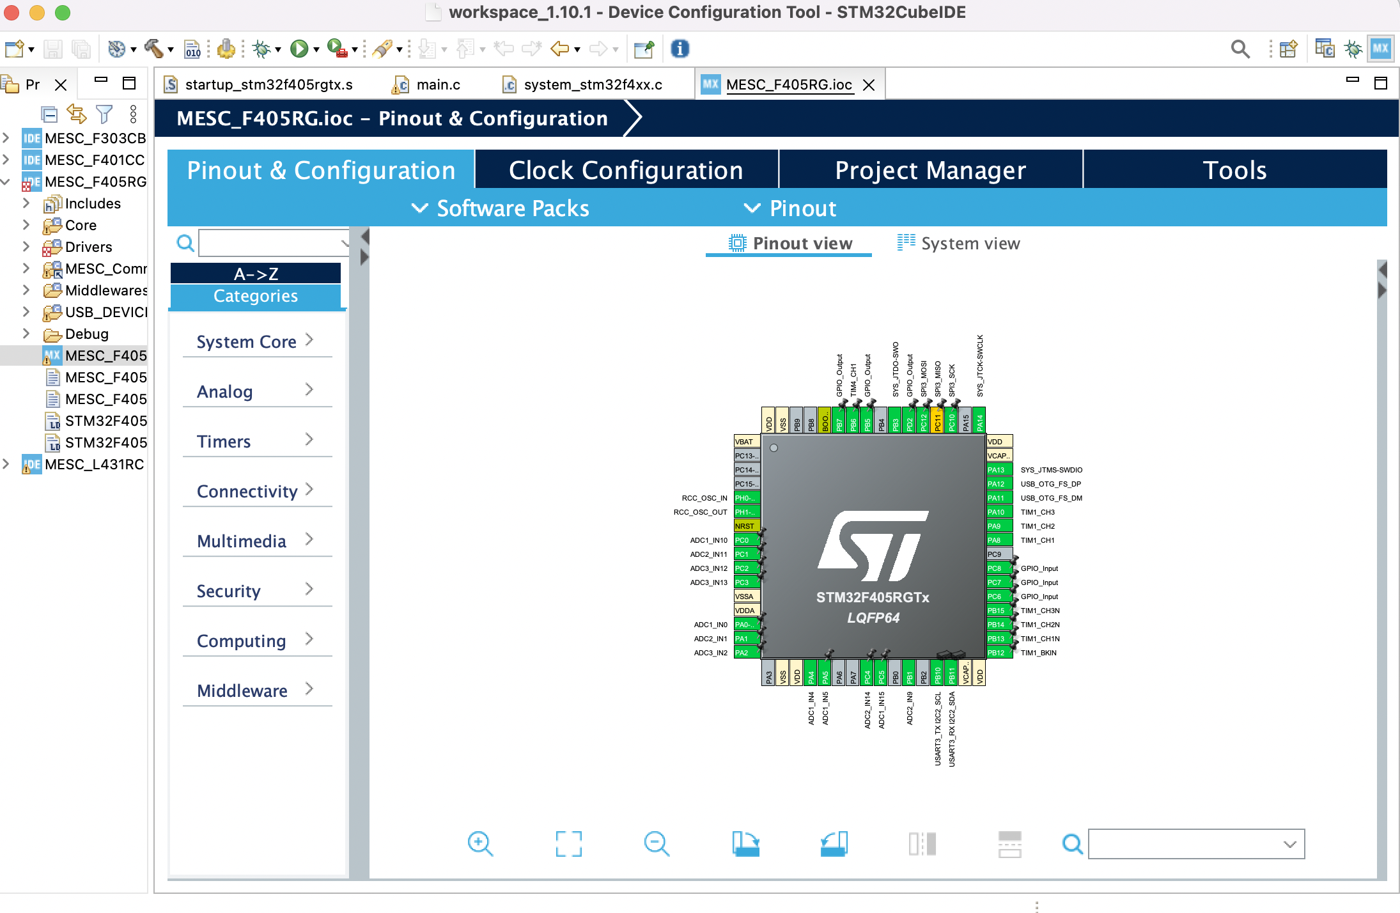
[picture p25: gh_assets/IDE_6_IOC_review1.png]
View pin functions


## Debugging -- getting started

To connect up your pill, you will use the abundantly available ST-LINK V2 debugger, and get connected like this:

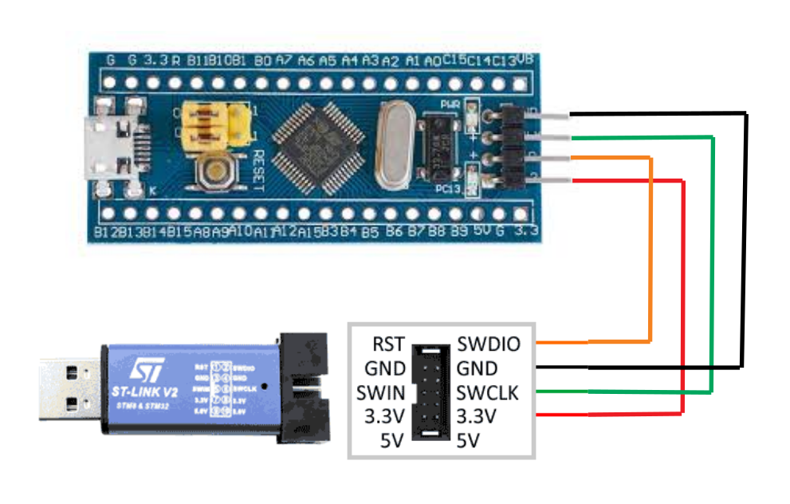
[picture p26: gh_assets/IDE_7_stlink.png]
ST-LINK pin connections


There are a couple of settings to watch out for in the configuration of the debugger. Make sure these parameters are set up:
Configure the debugger

There are a couple of settings to watch out for in the configuration of the debugger. Make sure these parameters are set up:
Configure the debugger

Once your st-link is connected and the debugger is configured you can get started by hitting this button. Sometimes you have to use that button's pulldown menu to select the debugging style that you want: 
ST-LINK pin connections

## Debugging -- what to do next

There are approximately 10<sup>5</sup> google results for [STM32cubeIDE debugging](https://www.google.com/search?q=stm32cubeide+debugging). Do your best.

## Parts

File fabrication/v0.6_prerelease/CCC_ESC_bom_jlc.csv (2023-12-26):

Comment | Designator | Footprint | LCSC Part #
47pF | C29,C30,C31 | C_0603_1608Metric | C1671
1nF | C14,C15,C16,C22,C23,C24 | C_0603_1608Metric | C1588
3.3nF | C19 | C_0603_1608Metric | C1613
10nF | C25 | C_0603_1608Metric | C57112
100n | C6,C7,C17,C20,C21,C26,C27,C28 | C_0603_1608Metric | C14663
100nF | C5 | C_0805_2012Metric | C342865
1uF | C18,C32 | C_0603_1608Metric | C15849
10uF | C1,C2,C3,C8,C9,C10,C11,C12,C13 | C_0603_1608Metric | C96446
470nF | CX11,CX12,CX13,CX14,CX15,CX16,CX17,CX18,CX19,CX20,CX21,CX22,CX23,CX24,CX25,CX26,CX27,CX28,CX29,CX30,CX31,CX32 | C_1210_3225Metric | C192761
D_Small | D4,D5,D6 | D_SOD-323 | C191023
LED | D9 | D_0603_1608Metric | C72041
US1M | D1,D2,D3 | D_SMA | C412437
R100 | R37,R39,R41 | R_0603_1608Metric | C22775
R150 | R33,R34,R35 | R_0603_1608Metric | C22808
2R2 | R42,R68,R69 | R_0603_1608Metric | C22939
4R7 | R1,R2 | R_0805_2012Metric | C17675
4R7 | R43,R44,R45,R46,R53,R54,R55,R56,R57,R58,R59,R60,R61,R62,R63,R64,R65,R66 | R_0603_1608Metric | C23164 C23214
47R | R36 | R_0603_1608Metric | C23182
1k | R16 | R_0603_1608Metric | C21190
1k8 | R9,R28 | R_0603_1608Metric | C4177
2k2 | R13,R19,R20,R22,R23,R25,R26 | R_0603_1608Metric | C4190
3k3 | R6,R8,R11 | R_0603_1608Metric | C22978
8k2 | R15 | R_0603_1608Metric | C25981
10k | R12,R27,R47,R48,R49,R50,R51,R52 | R_0603_1608Metric | C25804
22k | R17 | R_0603_1608Metric | C31850
30k | R67 | R_0603_1608Metric | C22984
47k | R30,R31,R32 | R_0603_1608Metric | C25819
100k | R18,R21,R24,R70 | R_0603_1608Metric | C25803
150k | R5,R7,R10 | R_0805_2012Metric | C17470
220k | R29,R38 | R_0603_1608Metric | C22961
360k | R14 | R_0805_2012Metric | C17645
470R | RN2,RN3,RN5 | R_Array_Concave_4x0603 | C25510
10k | RN1,RN4 | R_Array_Concave_4x0603 | C29718
0.5mR | SHA1,SHA2,SHA3,SHB1,SHB2,SHB3,SHC1,SHC2,SHC3 | Shunt_2512_6332Metric | C349161
L6498DTR | U1,U2,U3 | SOIC-8_3.9x4.9mm_P1.27mm | C500658
NCS20034DR2G | U4 | SOIC-14_3.9x8.7mm_P1.27mm | C695777

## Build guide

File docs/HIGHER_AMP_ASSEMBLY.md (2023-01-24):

# MP2 Assembly and Testing: high amperage methods

Items to note if you plan to run the MP2 at high amperage
* If you're using a hot plate or oven, add bus bars first
* Design bus bars to attach to heavy gauge wire
* Avoid bending, see below
* The mosfests MUST get some form of heat sinking
* None of this is easy for a beginner

Soldering big bus bars to the MP2 board is challenging: the larger the bar, the more heat is dissipated from your soldering iron so smaller irons will not work; another issue is that if youre not careful it you can start tacking down your bar, the bar expands and puts a bending force on your PCB. In some cases this creates a dangerous situation where the PCB is bent and has an increased likelihood of breaking thea ceramic caps.

One method of soldering bus bars that works very well is to use a soldering oven or hot plate. Take the hot plate or oven up to ~270°C, let the bars, solder and PCB all come up to temperature and allow to cool slowly. Because the expansion coefficient of the PCB (which has a lot of copper) and your bars is very similar, heating them all to the same temperature seems to reduce PCB bending.

Some successful examples:

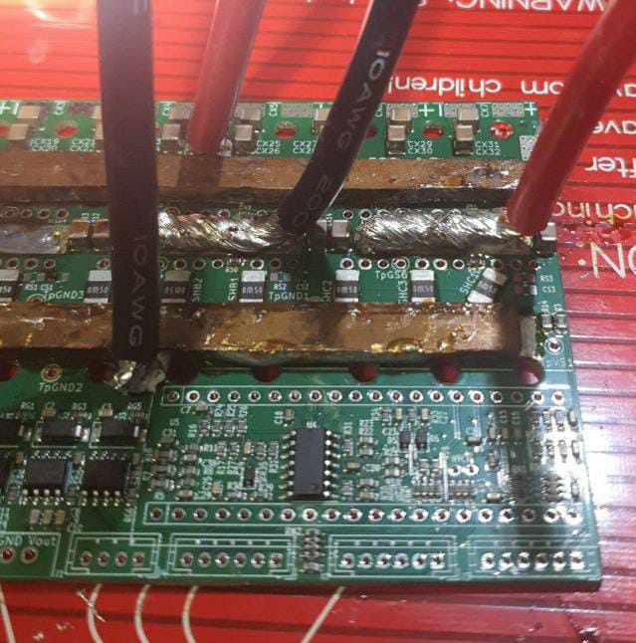
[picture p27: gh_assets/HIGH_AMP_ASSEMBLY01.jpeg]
example1


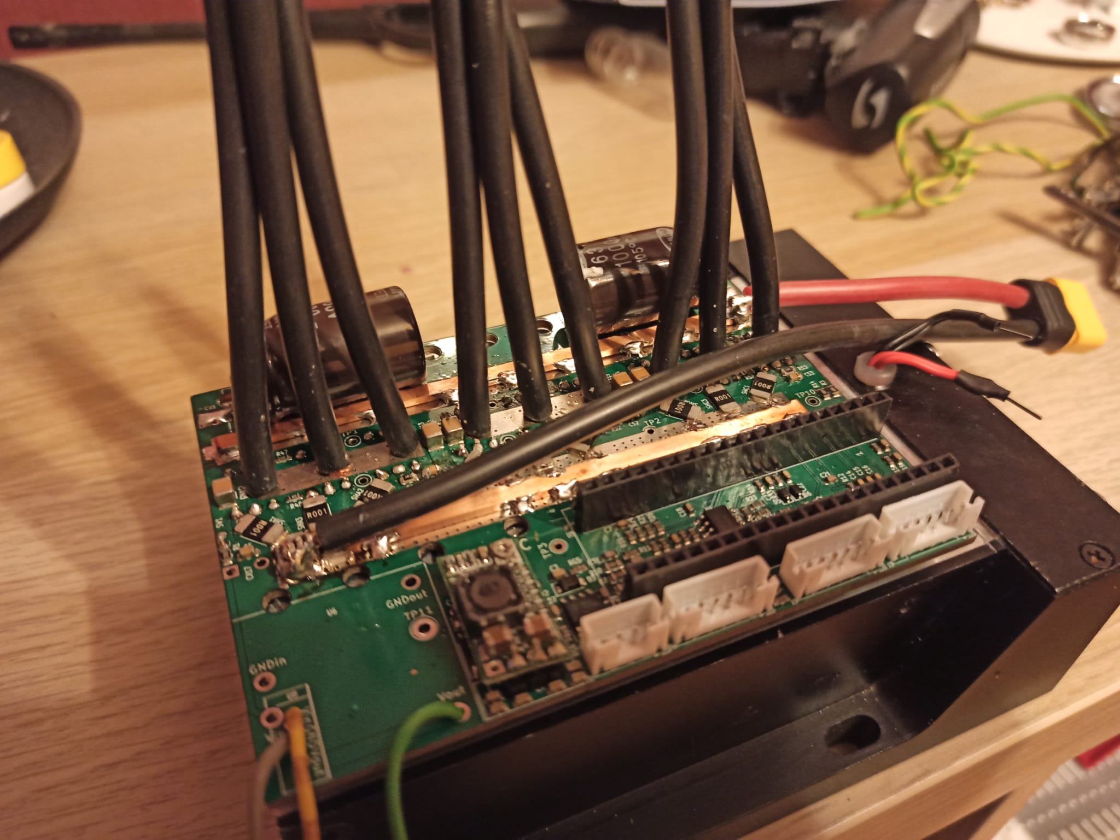
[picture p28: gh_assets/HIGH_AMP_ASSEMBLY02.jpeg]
example2


## How not to do it. 
In this case the problem is the large tabs of copper are likely to break off from the board if they receive lateral force. 

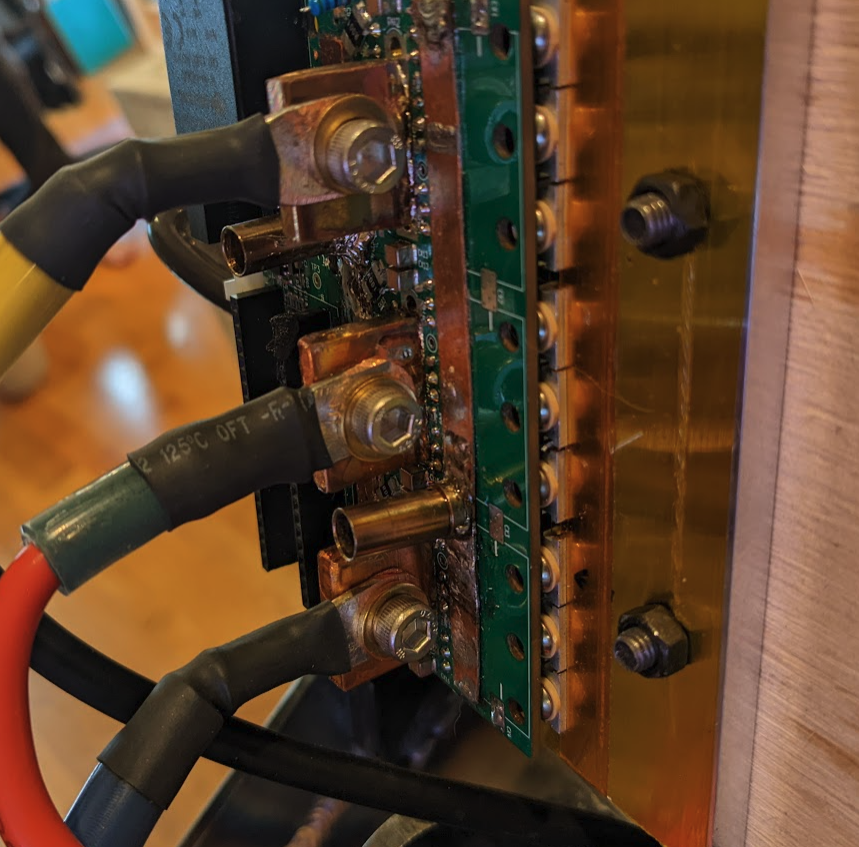
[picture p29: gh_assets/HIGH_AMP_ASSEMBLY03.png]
dont do this


## Department of overkill
This is an example of using laser cut copper to add copper bus bars that solder directly to wires. Soldering was done in an oven. 

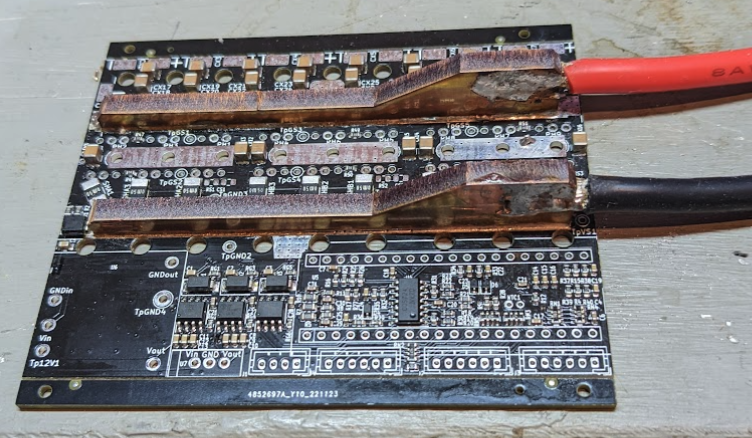
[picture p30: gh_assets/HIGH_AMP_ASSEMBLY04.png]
laser cut busbars


Messing with heat sinks sucks as much as all the other assembly. In this case laser cut aluminium was used, and then threaded to receive the heatsink bolts and "High-Strength High-Temperature PEEK" bolts were used for attaching to heatsink plate. PEEK is type of plastic and reliable in harsh environments up to 260° C. The blue stuff is 3M thermal pad (Mfr# 5583S-10). Normal human beings use kaptan tape and M3 insulation grommets. 

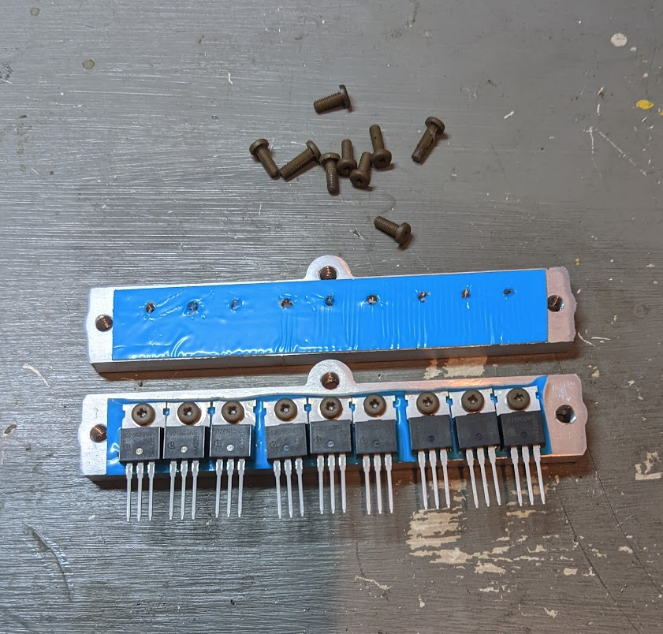
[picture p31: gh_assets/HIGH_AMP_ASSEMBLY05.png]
laser cut heatsinks


Final assembly with 2.5mm solid wire supports that have been soldered to threaded, copper pads. 
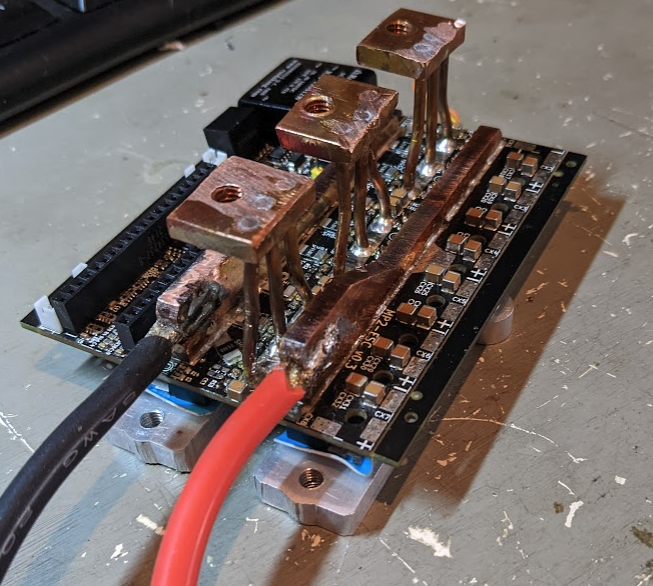
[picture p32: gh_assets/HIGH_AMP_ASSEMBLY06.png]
assembly


In addition to the added expense the downside of this method is soldering in all the MOSFETs with the big bus bars and phase wiring already in place is overly complicated.

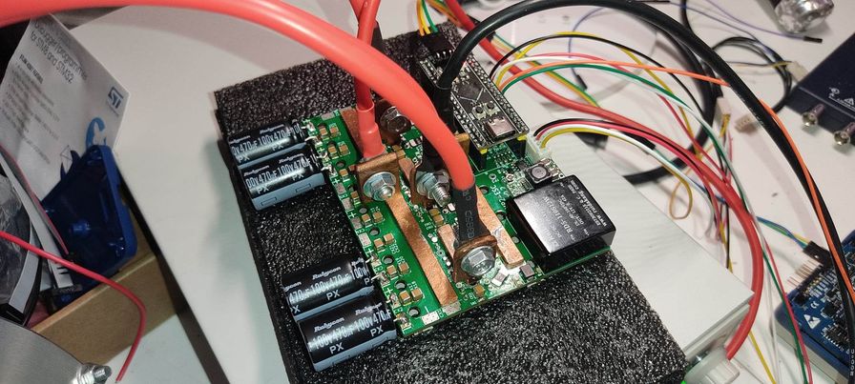
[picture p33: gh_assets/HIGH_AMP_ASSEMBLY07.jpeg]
assembly

Nicely done.

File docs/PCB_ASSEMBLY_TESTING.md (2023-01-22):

# MP2 Assembly and Testing

## MP2 PCB assembly
The following is not a step by step guide for finishing the MP2 but it still may be useful for people putting together their first PCB. 

Note: in this assembly we have not added any extra copper along the bus bars which is a common practice to increase the total amount of amperage used for these boards. Adding thicker bus bars is shown here [[LINK]](../docs/HIGHER_AMP_ASSEMBLY.md). However, **we recommend that if you are going to solder bus bars on your MP2 that you begin with that step first**. 

There are MANY tutorials on how to solder and hopefully this is not your first rodeo. At a minimum you are going to need a high wattage soldering iron, decent quality solder, hopefully some flux remover and a multimeter to be able solder this board. 

Looking at the top side of the board, it tends to be easiest to solder in the shorter parts first (so they rest flat on the bench when getting soldered in. So a possible order is:
* JST connectors
* 12V to 5V DC-DC converter
* the larger 12V DC-DC converter
* 20 pin headers

When doing the 20 pin headers...

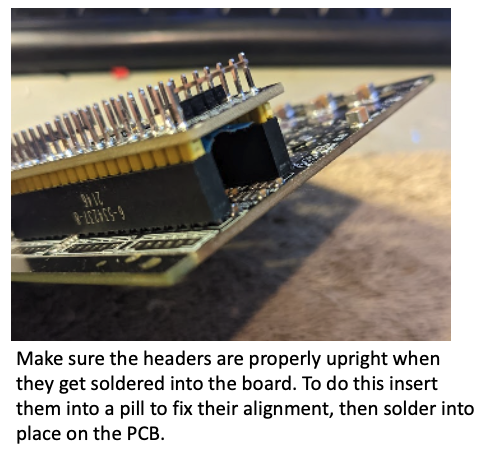
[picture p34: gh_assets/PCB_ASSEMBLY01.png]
header pin alignment


Another suggestion:

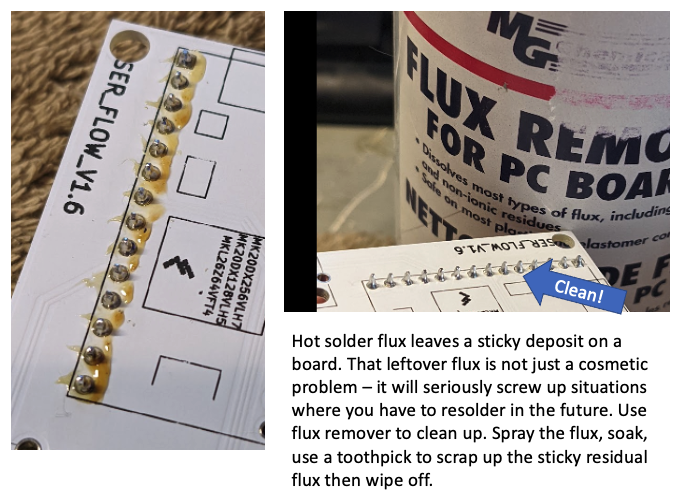
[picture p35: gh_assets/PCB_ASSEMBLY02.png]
use flux remover


The 12V-5V DC converter sits funny:

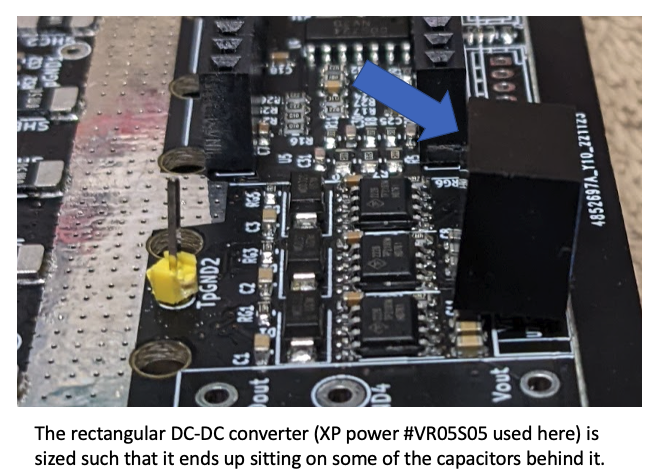
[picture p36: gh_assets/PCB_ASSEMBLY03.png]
DC-DC sits funny


Heat shrink tubing is your friend!

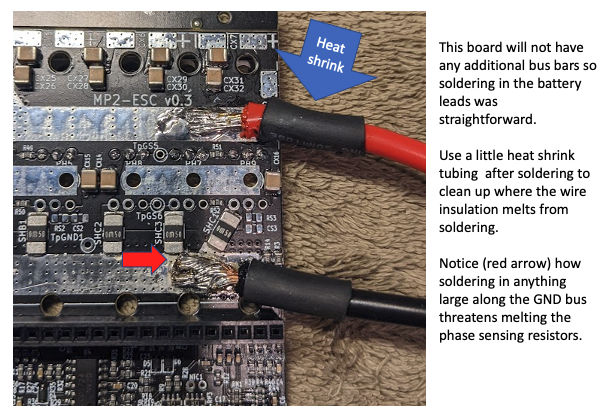
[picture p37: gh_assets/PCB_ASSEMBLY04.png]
soldering Vbat and GND


Use precision:

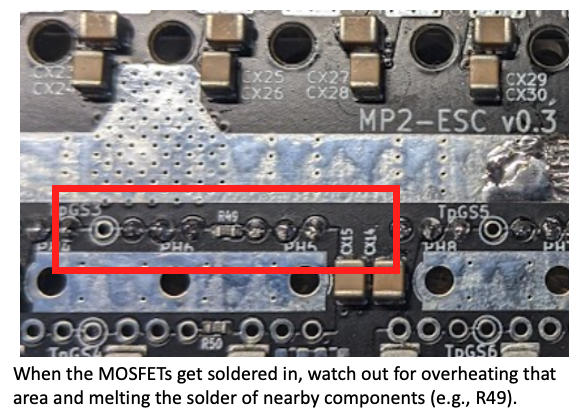
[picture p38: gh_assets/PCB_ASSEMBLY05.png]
watch out for components

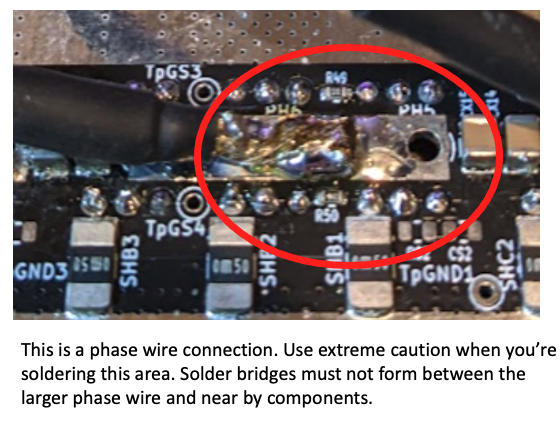
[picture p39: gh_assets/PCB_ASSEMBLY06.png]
watch out for solder bridges


**NOTE:** These pics are included to talk about soldering issues, **BUT BE ADVISED WE STRONGLY RECOMMEND** users take advantage of the three holes on each phase to solder in larger wires and get improved current sharing with the MOSFETs. A better example is shown here [[LINK](../gh_assets/HIGH_AMP_ASSEMBLY02.jpeg)] and take a look at [THIS FUTURE DOCUMENTATION] for other higher amperage connections. 

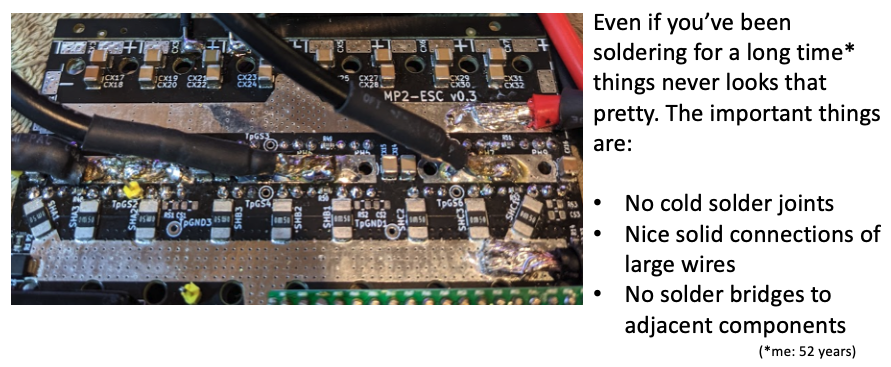
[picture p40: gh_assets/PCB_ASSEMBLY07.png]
it aint pretty


## MP2 continuity testing
Before you're finished with soldering be sure to do some important testing of your board. One set of tests involved using a continuity checker on your multimeter. This is a **short video** to help you get started:

MP2 continuity checking (https://www.youtube.com/watch?v=L9bziAqBU64)

Once your set up for testing run through the following tests:

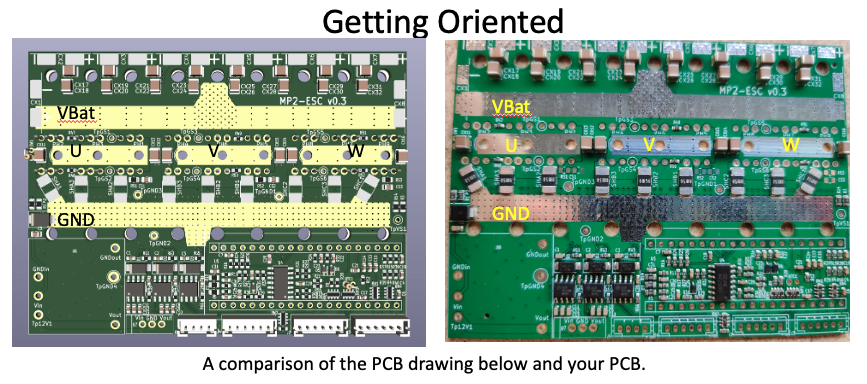
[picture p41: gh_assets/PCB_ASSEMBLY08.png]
pcb continuity chart


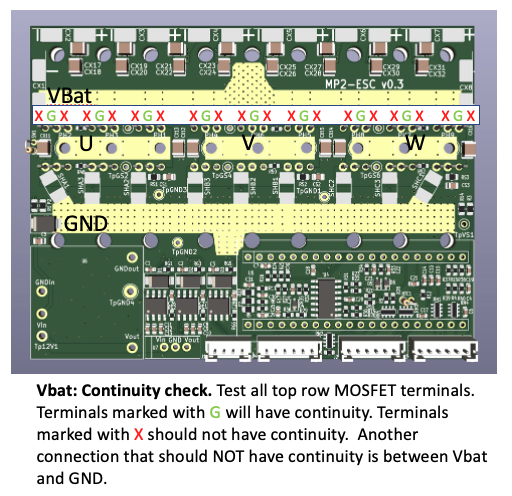
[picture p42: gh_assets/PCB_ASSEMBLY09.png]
VBat continuity check


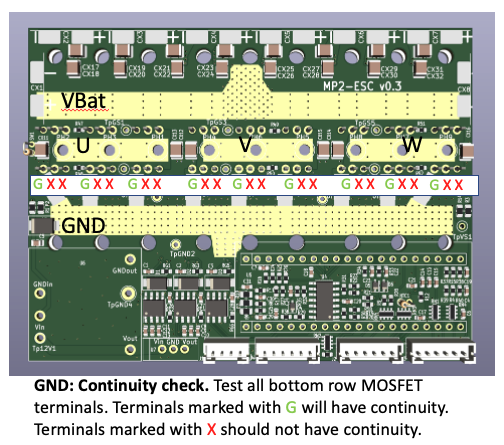
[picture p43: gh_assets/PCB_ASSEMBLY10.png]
GND continuity check


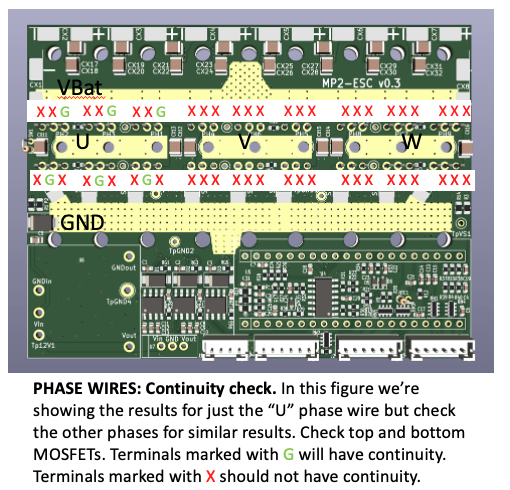
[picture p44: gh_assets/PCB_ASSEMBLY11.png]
Phase wire continuity check


## MP2 resistance testing
Since you have your multimeter out there are some other useful measurements to take. These tests can vary based on what type of meter you have. Also sometimes the readings will take a while to settle down to the final value.

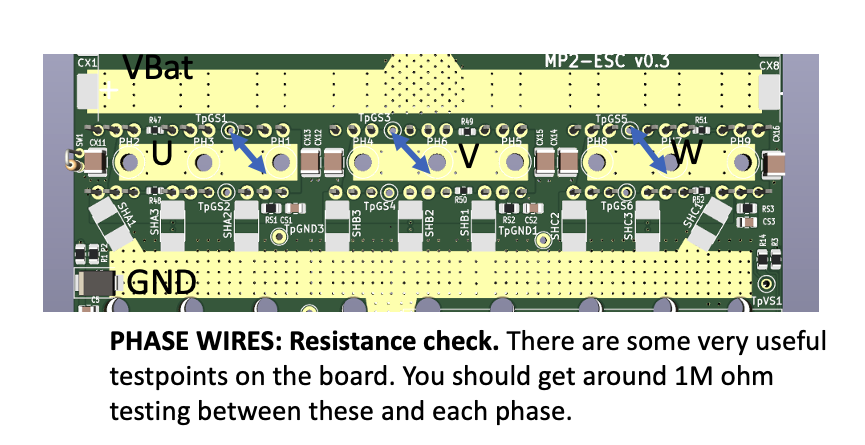
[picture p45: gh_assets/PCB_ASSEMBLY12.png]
Phase wire resistance check1


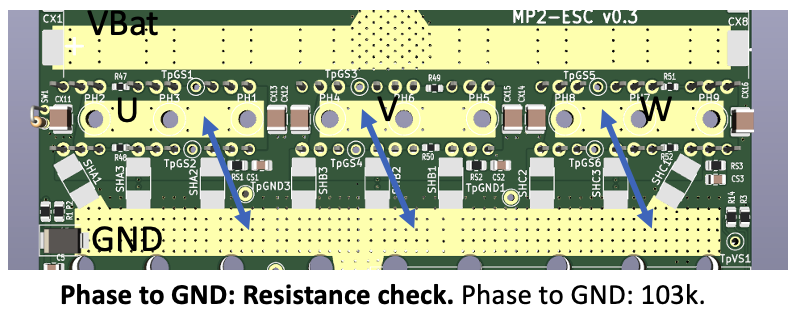
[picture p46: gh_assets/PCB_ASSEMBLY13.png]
Phase wire resistance check2


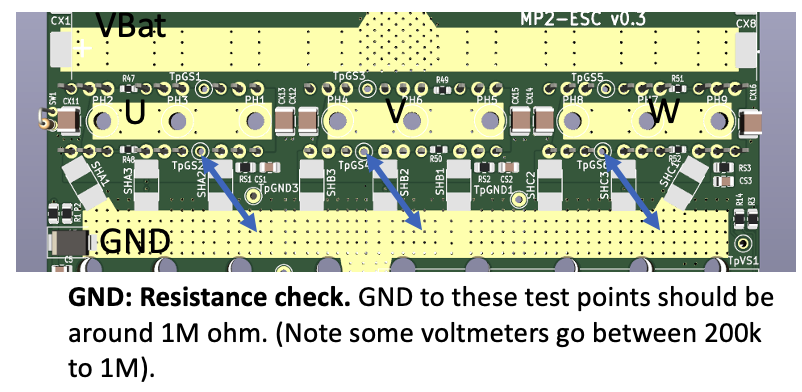
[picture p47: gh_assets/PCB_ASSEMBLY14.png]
Ground to testpoint check


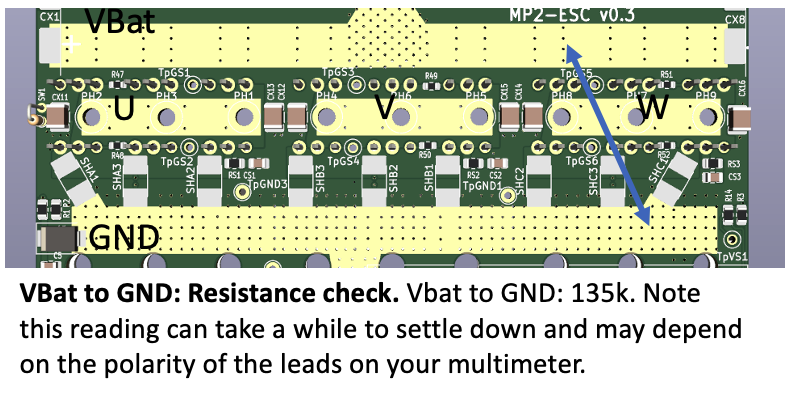
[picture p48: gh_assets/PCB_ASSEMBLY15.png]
Ground to VBat check


## MP2 powering up

Hopefully you have experience powering up a PCB for the first time, but here a subset of things you can do when starting up the MP2. 

Connect a switch or put in a jumper over on the [middle-left side of the board](../gh_assets/PCB_ASSEMBLY16.png). Then: 

* First remove the pill from the MP
* Connect your multimeter to GND
* Apply power to VBat
* Note that in some cases the DC-DC converter wont activate at <42 volts
* Test for voltages on the points shown...

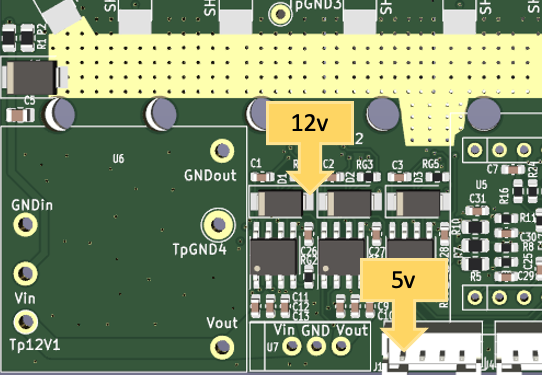
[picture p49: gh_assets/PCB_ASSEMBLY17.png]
Voltage check


If youre voltages look good, power off, plug in the pill and hopefully you'll see a comforting power light on the pill.

## MP2 loading the firmware. 

* Disconnect the F405 pill from the MP2 board;
* Search the internet and break a record ($2USD) for the most inexpensive ["st-link v2"](https://www.google.com/search?q=st-link+v2) in existence;
* Search on ["STM32CubeProgrammer software STM32"](https://www.google.com/search?q=STM32CubeProgrammer+software+STM32&oq=STM32CubeProgrammer+software+STM32), download and install the programmer code;
* Search, find, 'request from a friend' or compile for yourself a copy of the VESC bin file for the F405 pill;
* Search ["st-link V2 STM32 programming bluepill"](https://www.google.com/search?q=st-link2+STM32+programming+bluepill) to learn how to [connect](../gh_assets/IDE_7_stlink.png) your st-link to a pill;
* Use the STM32CubeProgrammer to upload the bin file;
* Search, find, 'request from a friend' or compile for yourself a copy of the VESCtool;
* Do not plug the pill into the MP2, upload the VESC firmware to the pill, connect the USB and start VESCtool;

Select "Connection" on the left hand side of VESCtool. If you see this on your screen:
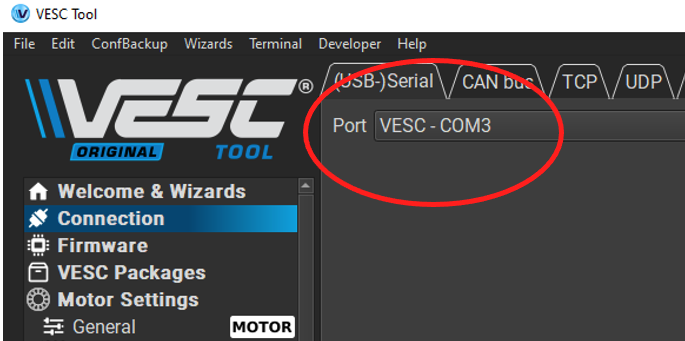
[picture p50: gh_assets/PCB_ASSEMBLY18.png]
VESC tool


That is good news.

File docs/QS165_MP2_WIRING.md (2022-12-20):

# IGNORE MOST OF THIS MATERIAL 
**At present the main problem with these connections is there is no flex between the wiring and the board. These pics are included for the purpose of ridicule and discussion. ** 

## Wiring QS165 to MP2

**MP2 temporarily mounted into position.**

This position will be nice because heat block will be forward facing. 

MP2 mounts

---
**Lengthened the stock QS wires.**

Big fan of heat shrinking TF out of everything. 

QS165 side view

---
**Reused the stock rubber boot from QS for my wires.**

Rubber boot

---
**Top view of the battery box.**

Connectors are in series and in potted epoxy.

Battery box

---
**5mm thick blocks of copper are soldered in for phase wires.**

Blocks span the length of phase connection area and are threaded to receive M5 bolts. Bullet connectors attach to Vbat+/-

Battery terminals

---
**Male end of bullet connector.**

Bullet connector

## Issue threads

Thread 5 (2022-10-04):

Improve docs

jsam, 2022-10-04:
Hey,

Just found this really cool project and wanted to drop in and say thank you for open sourcing it!

Do you think its possible to improve the docs a bit for not-so-experienced hardware people.

Few things I see it would help a lot is maybe:
  1) Adding a `bom` file and instructions on ordering it from JLCPCB
  2) Assembly instructions
  3) Instruction on building/hooking up all the different modules
  4) Contribution guidelines / roadmap

Thank you!
Sam.

badgineer, 2022-10-04:
Hi.
Thanks for the interest

I thiught there is a bom, i will regenerate it when i get a chance (very
busy atm).
The same for module list - we have some tested some not yet tested we can
recomment.

Aslo, more info there will be on the ES thread and hopefully in a
half-useful readme.

https://endless-sphere.com/forums/viewtopic.php?t=117045

We are in the testing phae cureently btw, slowly adding improvements
resulted from testing to the design.

Also heavily working on software in paralell (not me, other people more
softwarw savvy )

If yiu have improvement ideeas, feel free to post to es thread :)

Br,

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

badgineer, 2022-11-03:
Hi.
Started taking documentation more seriously. See Readme :)
Haven't added guides for assembly here, hope to add some in the ES thread I linked to. (when I finally get the time to assemble my v01 prototype)

Best Regards!

badgineer, 2023-01-22:
Hi.
So documentation is still not perfect - and it will probably never be.
But I think its good enough that I can close this :)

Best Regards.

jsam, 2023-01-26:
Thanks a lot!

Closed 2023-01-22.

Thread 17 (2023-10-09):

OpAmp Gain Calculation

hkesoglu, 2023-10-09:
Hi!
It's really nice to see such a design. I am designing a circuit that will work with simplefoc and I am thinking of using bluepill. However, since I want it to operate at lower voltages and currents, there are too many unnecessary things in your design for my situation. I want to use the opamp part of your design. But I don't understand how you choose the resistor values.

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

When I examine the datasheet of cos724, I understand that you are using a Differential Amplifier. When I calculate it according to the calculations I found on the internet, your gain ratio is very low. I couldn't understand how it worked.

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

In my case, I need to set it to see 20A max. I calculate that when I choose 2mR it drops 20 * 0.002 = 40mV. Considering the ADC max voltage to be 3V (300mV for safety), I thought I should set it to something like 3000/40=75 gain ratio. What should I change the resistor values in your circuit to get a ratio like 75? Is it possible?

I'm also wondering why the R18 100kOhm resistor is connected to 3.3V? Is it to provide offset?
Or does it make a differential so that it does not exceed 3.3v?

Thanks.

badgineer, 2023-10-27:
Hi.
in very short - R18 provides offset, yes.
offset * gain ~1.6 V (the middle of 0 and 3.3. this is so we can have full sine wave without negative voltage source on opamp. zero amps thus is 1.6V
gain is about 22 - full current range that can be read is almost 450A.

if you only want 20A max, you can use a bigger shunt, and size the opamp so the max current you can read is somewhere in 30-40 range.

Closed 2024-03-26.

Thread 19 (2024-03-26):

Gerber or BOM not updated for 0.6

DsSoft-Byte, 2024-03-26:
When trying to get a MP2-ESC V0.6 assembled on JLCPCB using the provided BOM, CPL and Gerber i get such an error.
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

DsSoft-Byte, 2024-03-26:
Im stupid, these are pads for caps

badgineer, 2024-03-26:
Hi there.
yes, these are parts not populated on purpose.
so are the snubber caps and resistors.
By the way, 0.6 is not tested, at least not to my knowledge. so if you find problems (or want to report success) get in touch.
There's an endless sphere thread you can post in.
Br,
badgineer

Closed 2024-03-26.

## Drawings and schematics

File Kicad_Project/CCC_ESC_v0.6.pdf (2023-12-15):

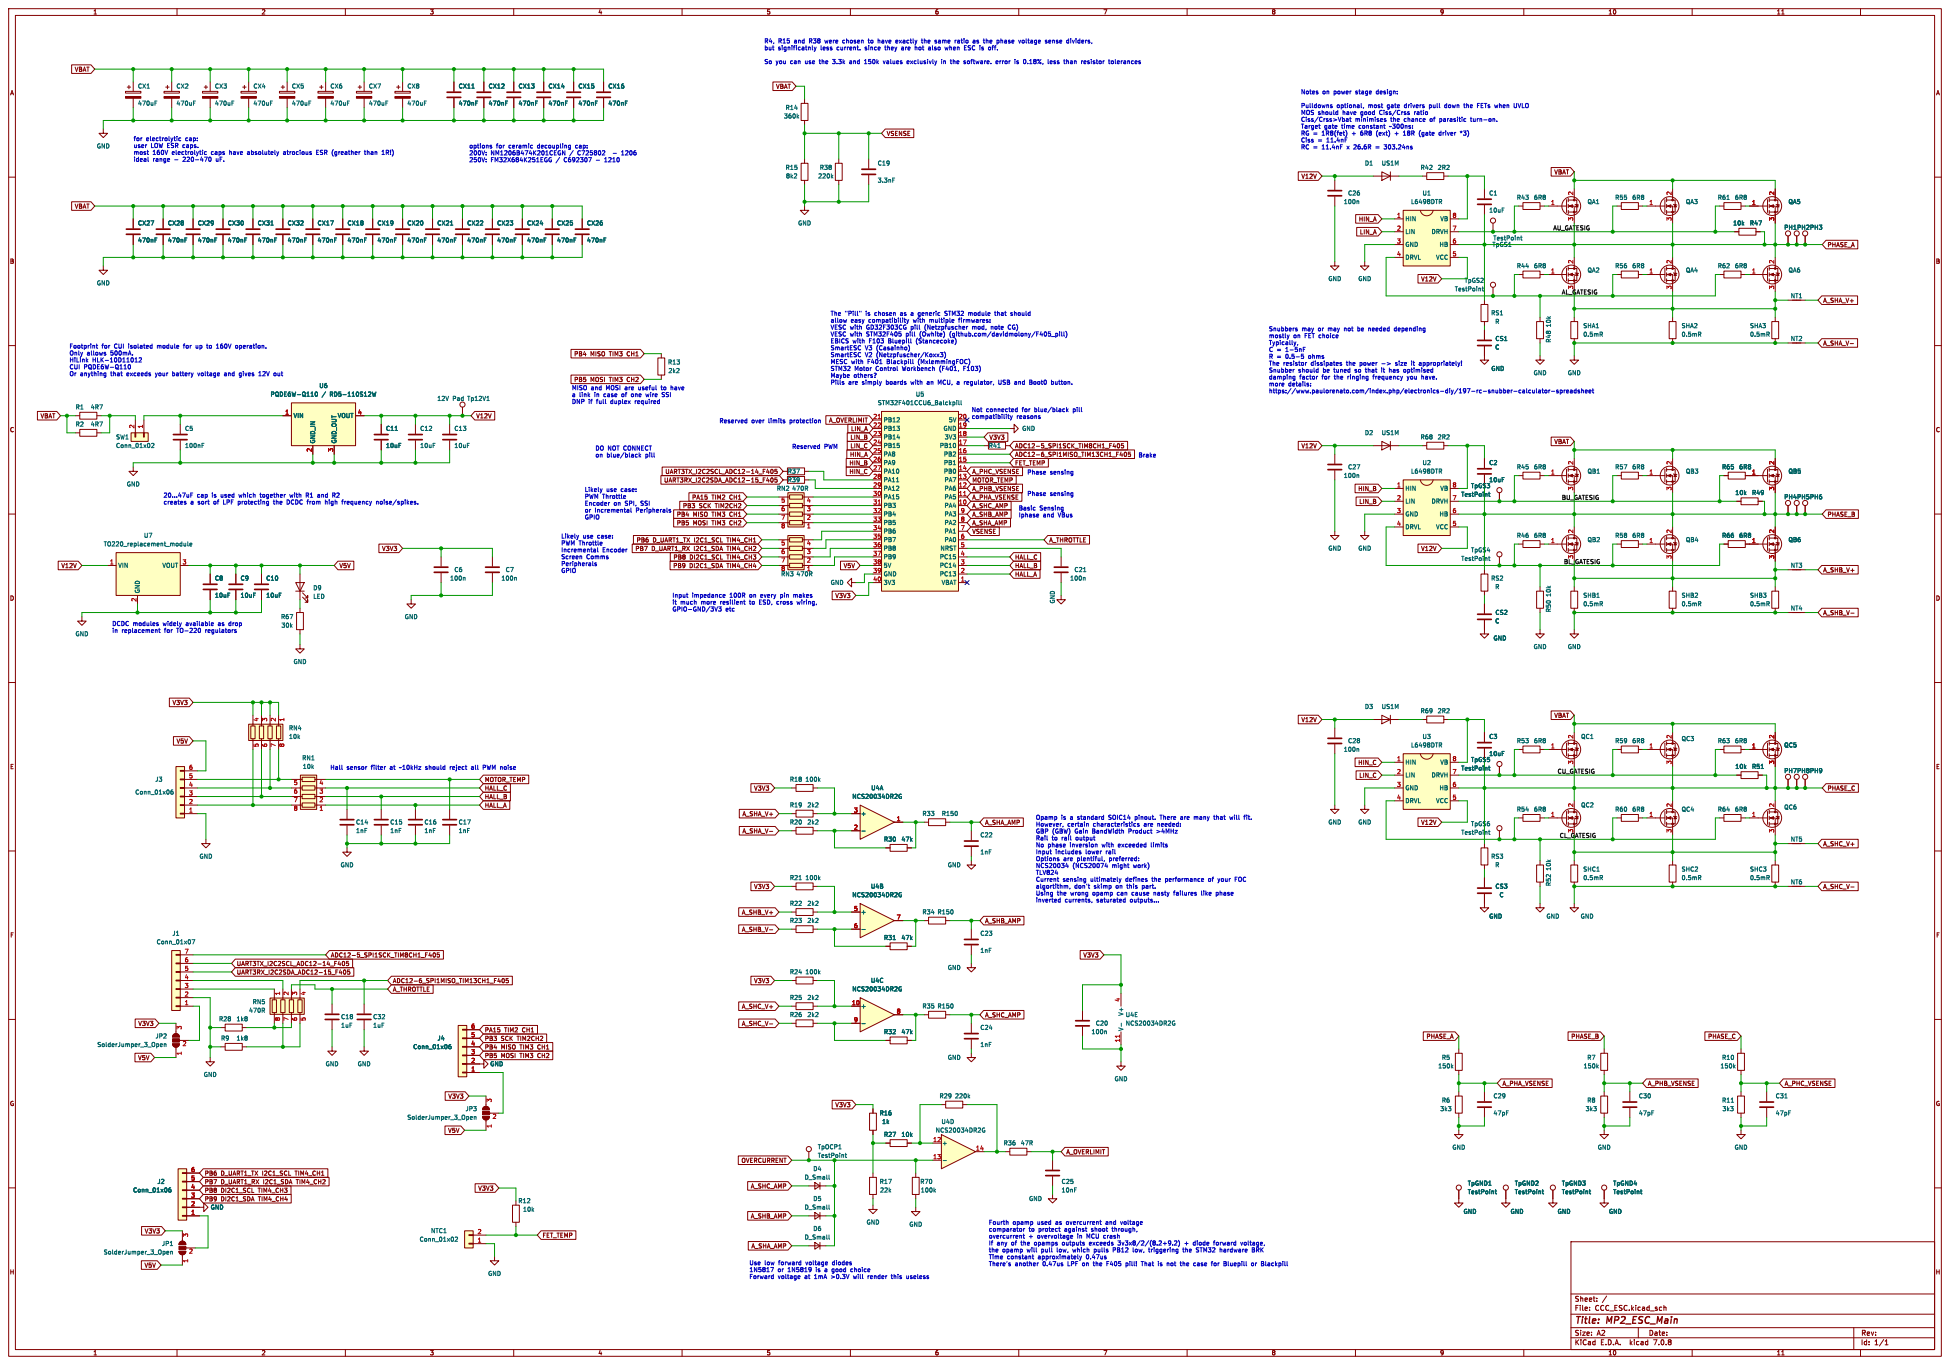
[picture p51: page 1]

Snubbers may or may not be needed depending

a link in case of one wire SSI DNP if full duplex required

Iphase and VBus Phase sensing

Likely use case: PWM Throttle

Hall sensor filter at ~10kHz should reject all PWM noise

Use low forward voltage diodes 1N5817 or 1N5819 is a good choice Forward voltage at 1mA >0.3V will render this useless

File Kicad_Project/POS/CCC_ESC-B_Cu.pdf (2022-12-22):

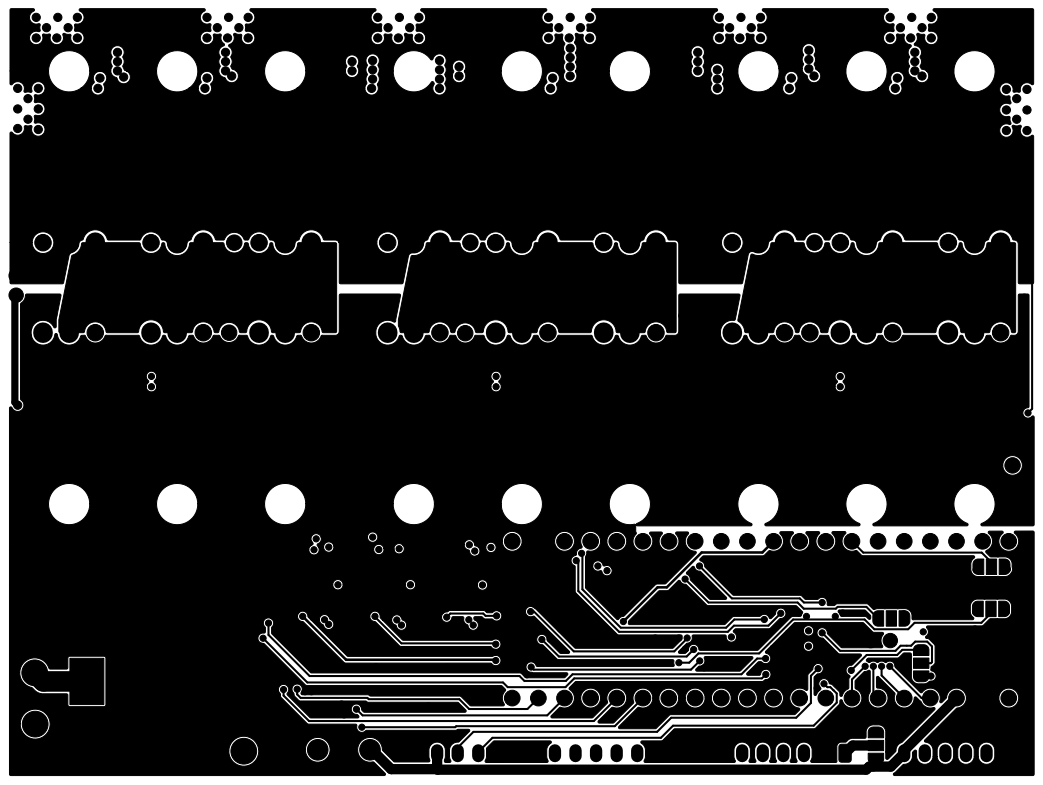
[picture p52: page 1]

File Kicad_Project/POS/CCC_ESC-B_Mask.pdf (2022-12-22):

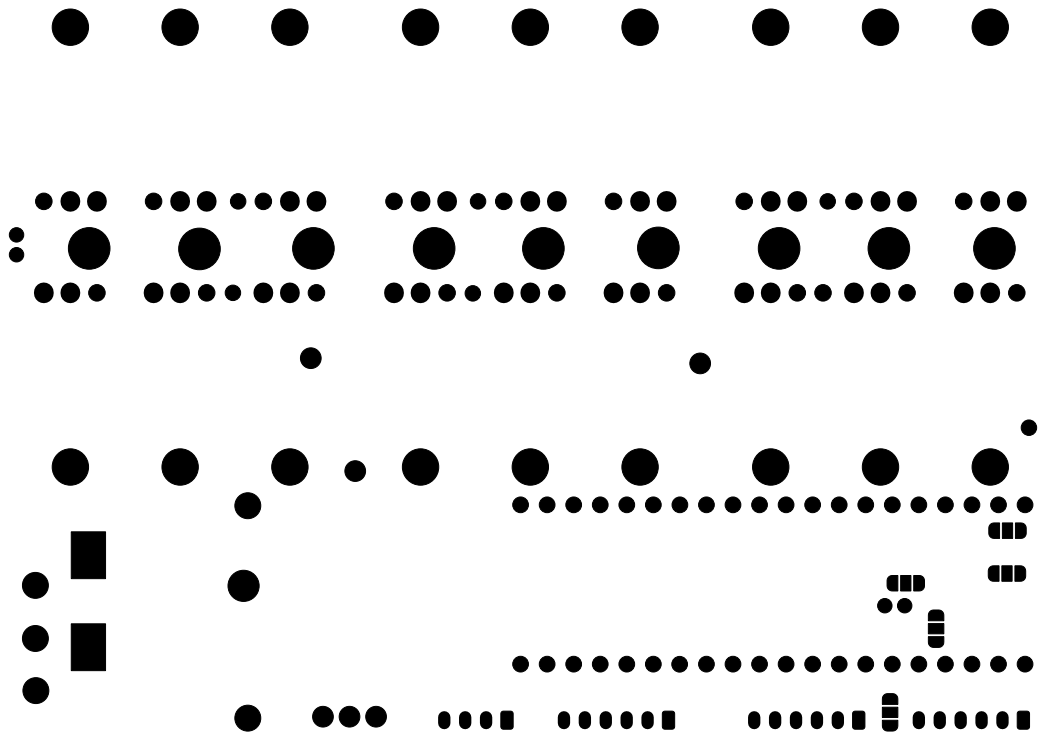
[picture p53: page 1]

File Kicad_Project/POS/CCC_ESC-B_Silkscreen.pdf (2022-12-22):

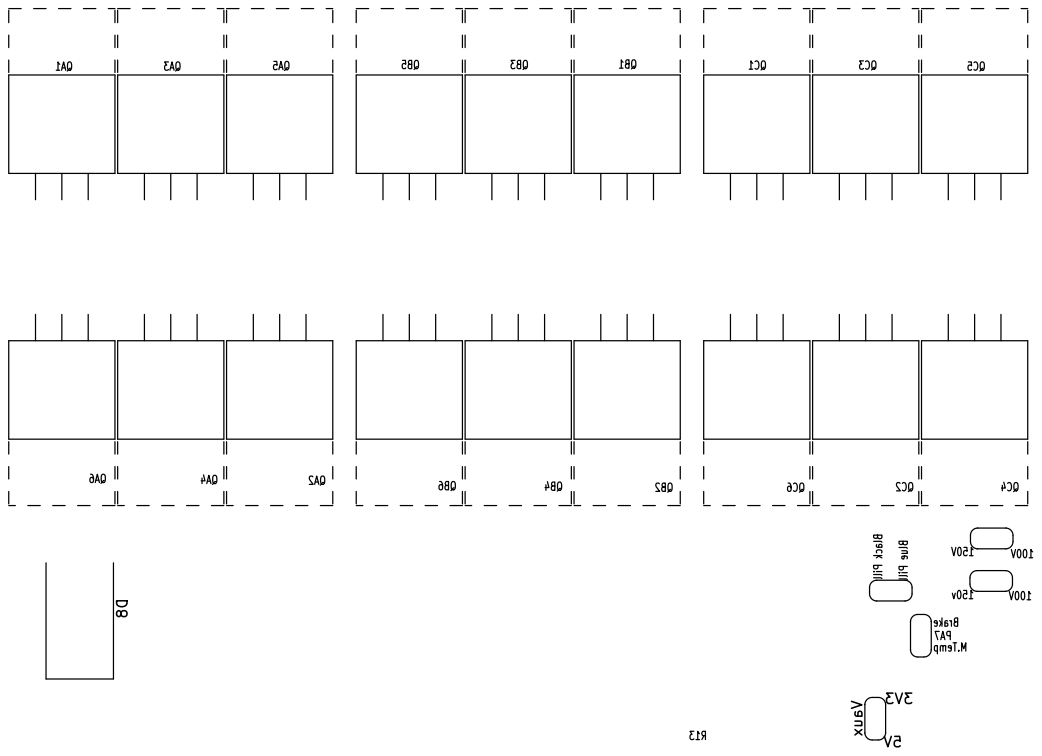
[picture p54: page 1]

3V3 QB4 QA3 QB5 QC6 QC5 QC4 Black Pill Blue Pill

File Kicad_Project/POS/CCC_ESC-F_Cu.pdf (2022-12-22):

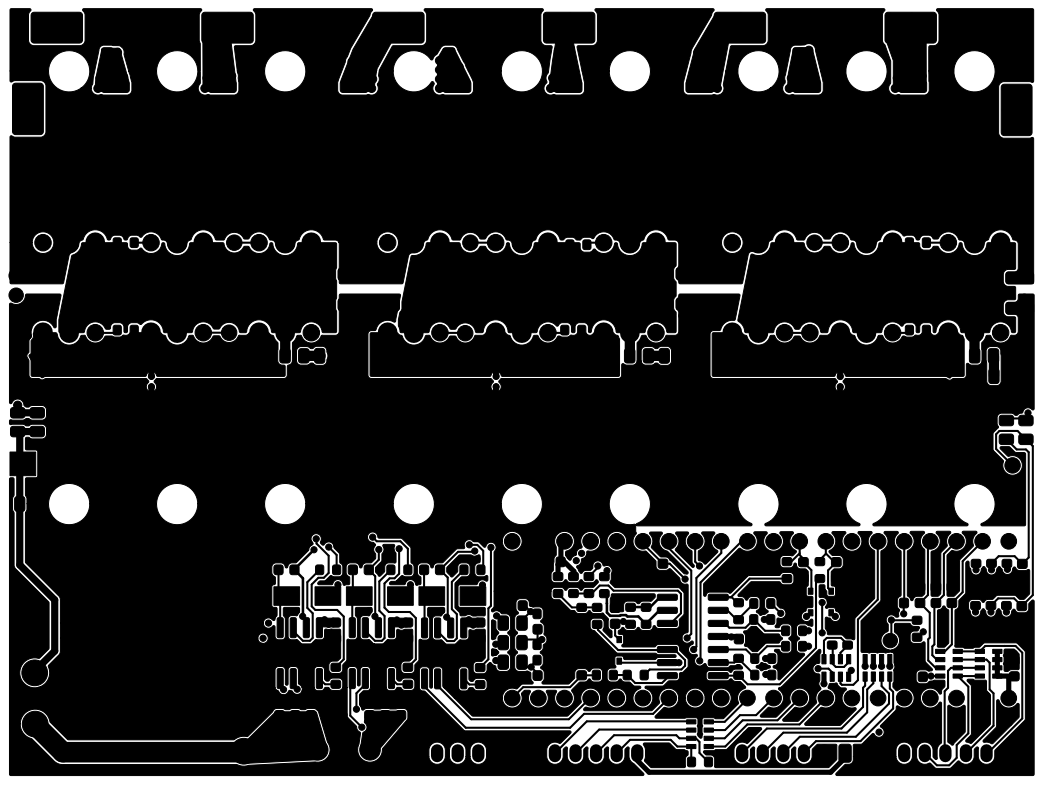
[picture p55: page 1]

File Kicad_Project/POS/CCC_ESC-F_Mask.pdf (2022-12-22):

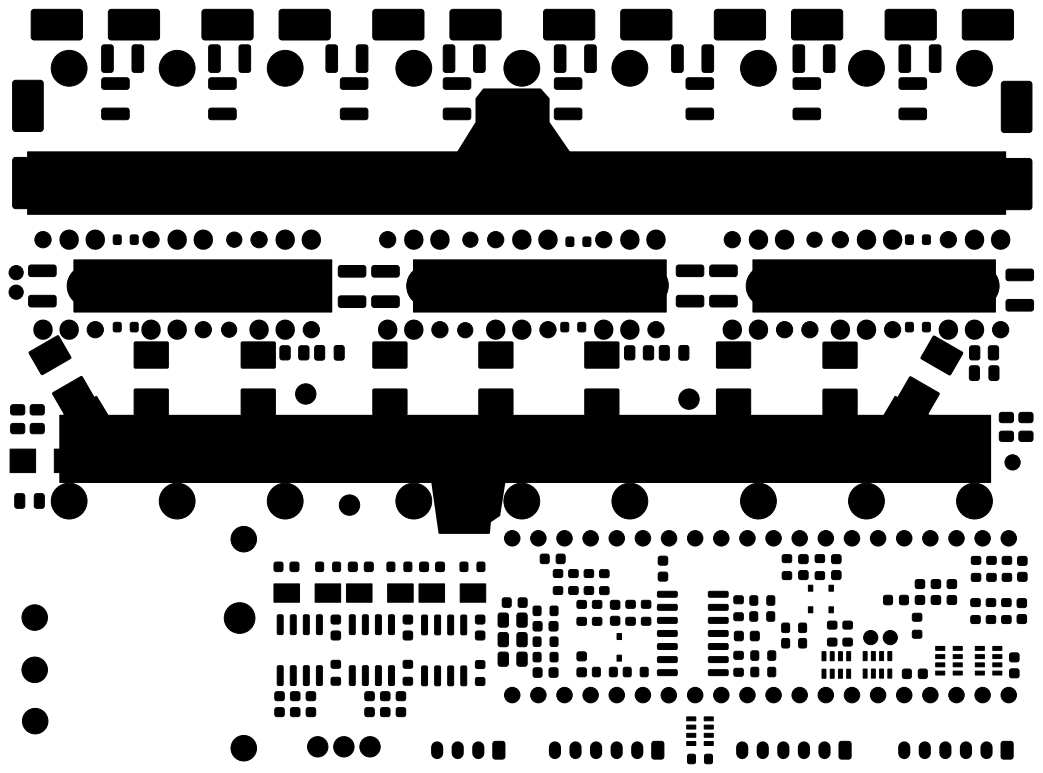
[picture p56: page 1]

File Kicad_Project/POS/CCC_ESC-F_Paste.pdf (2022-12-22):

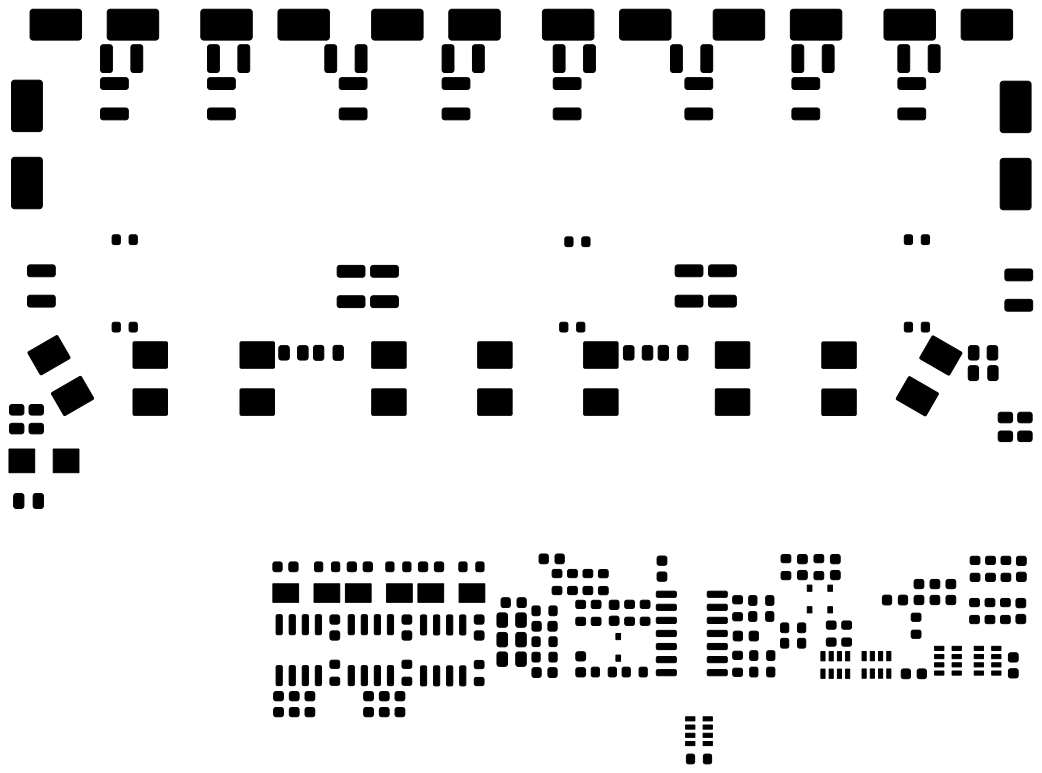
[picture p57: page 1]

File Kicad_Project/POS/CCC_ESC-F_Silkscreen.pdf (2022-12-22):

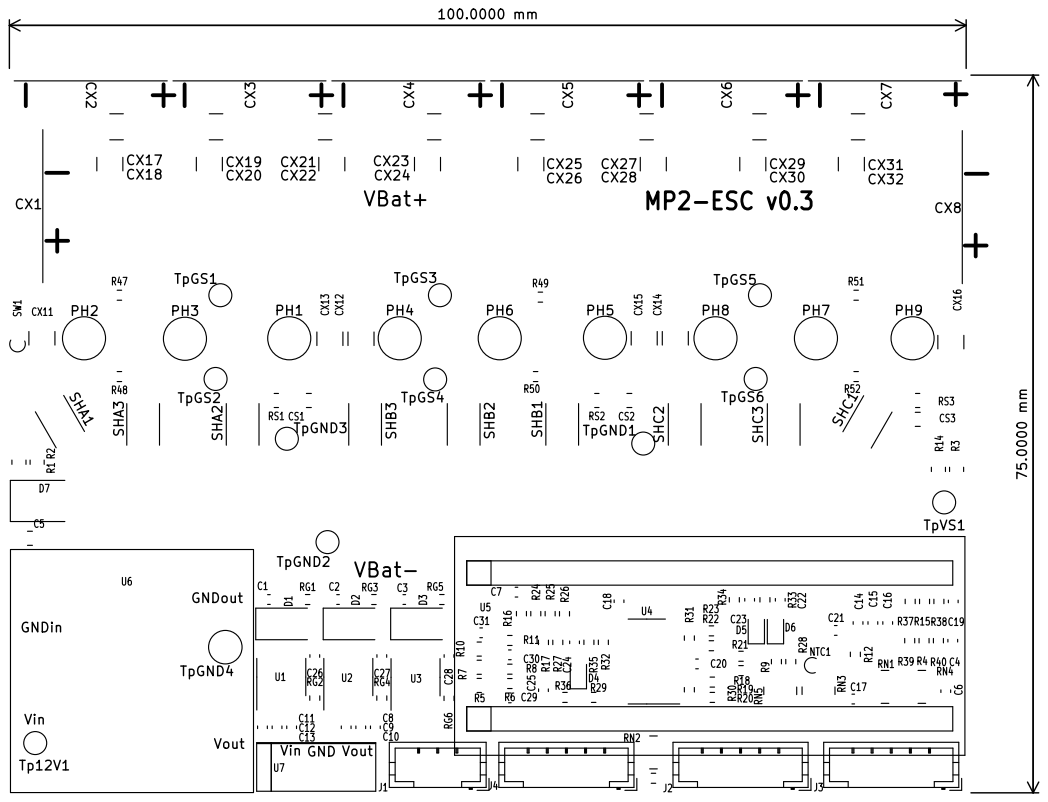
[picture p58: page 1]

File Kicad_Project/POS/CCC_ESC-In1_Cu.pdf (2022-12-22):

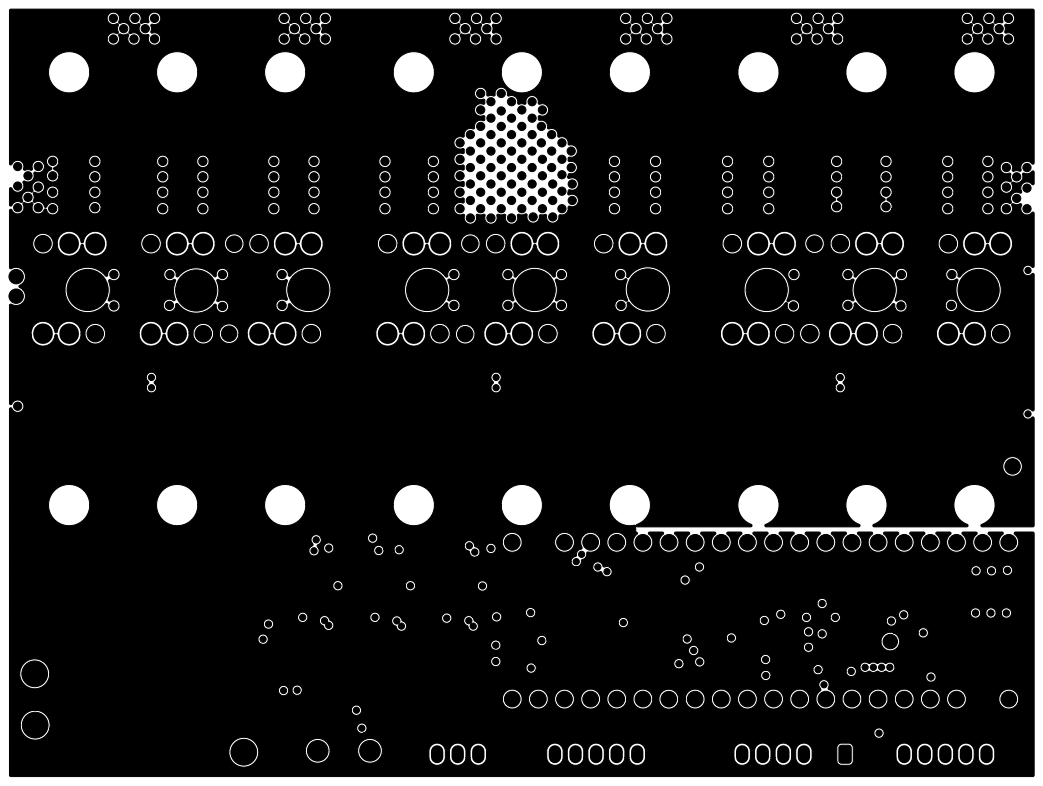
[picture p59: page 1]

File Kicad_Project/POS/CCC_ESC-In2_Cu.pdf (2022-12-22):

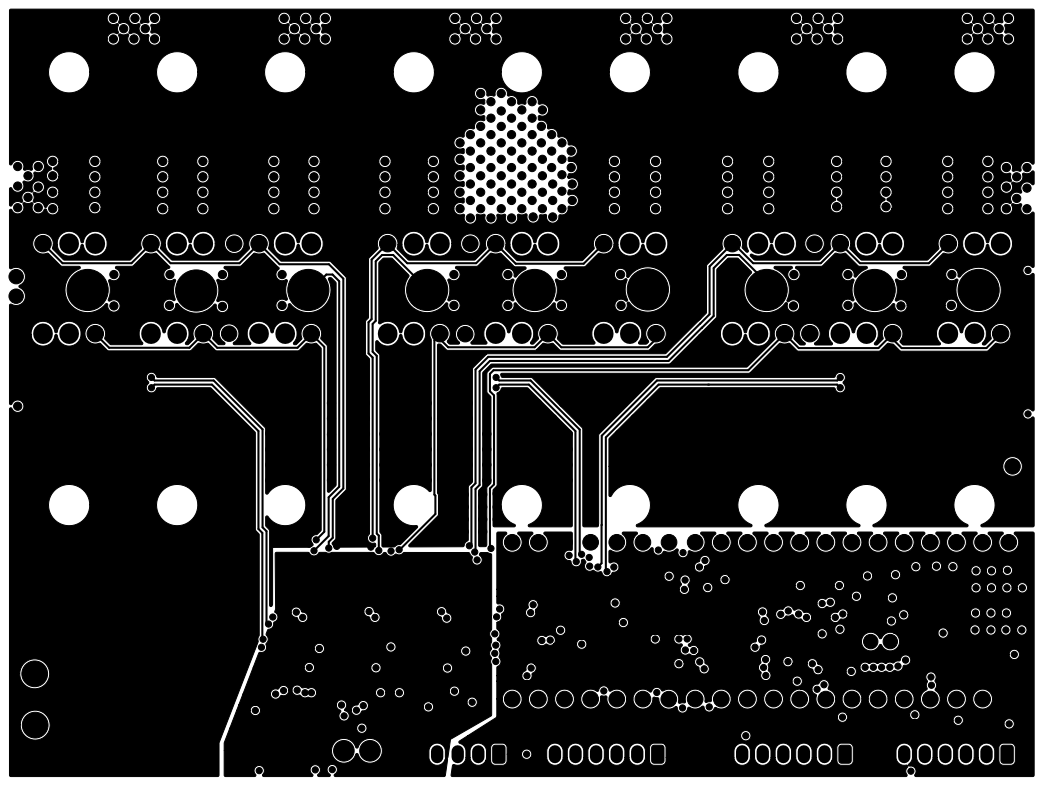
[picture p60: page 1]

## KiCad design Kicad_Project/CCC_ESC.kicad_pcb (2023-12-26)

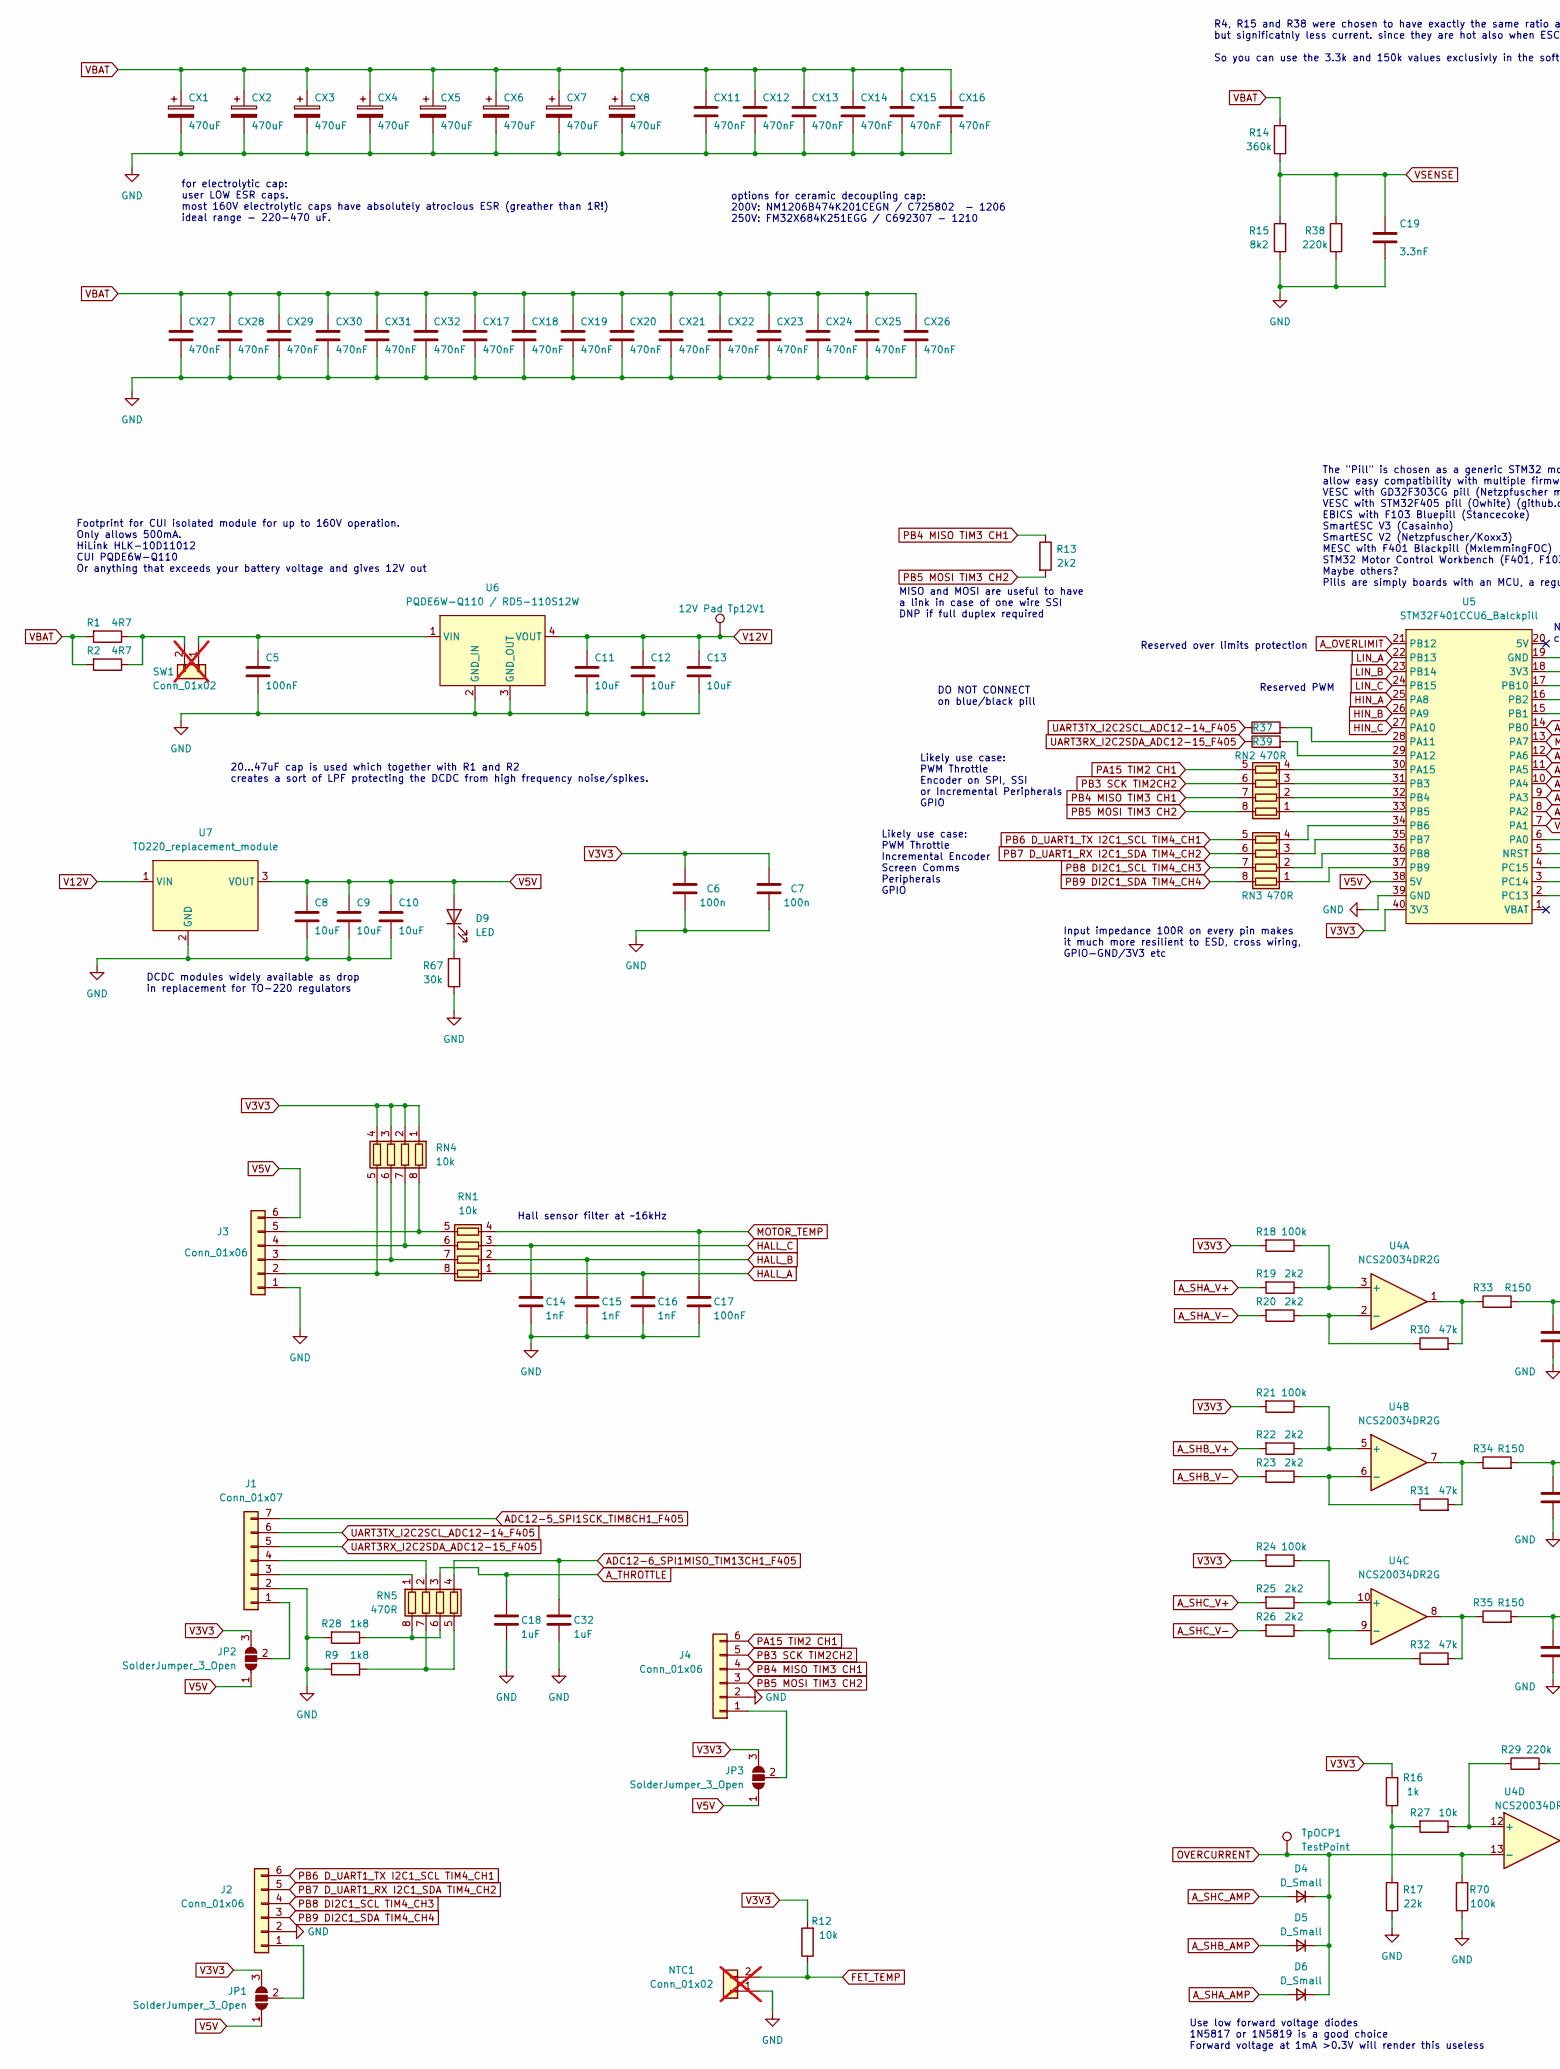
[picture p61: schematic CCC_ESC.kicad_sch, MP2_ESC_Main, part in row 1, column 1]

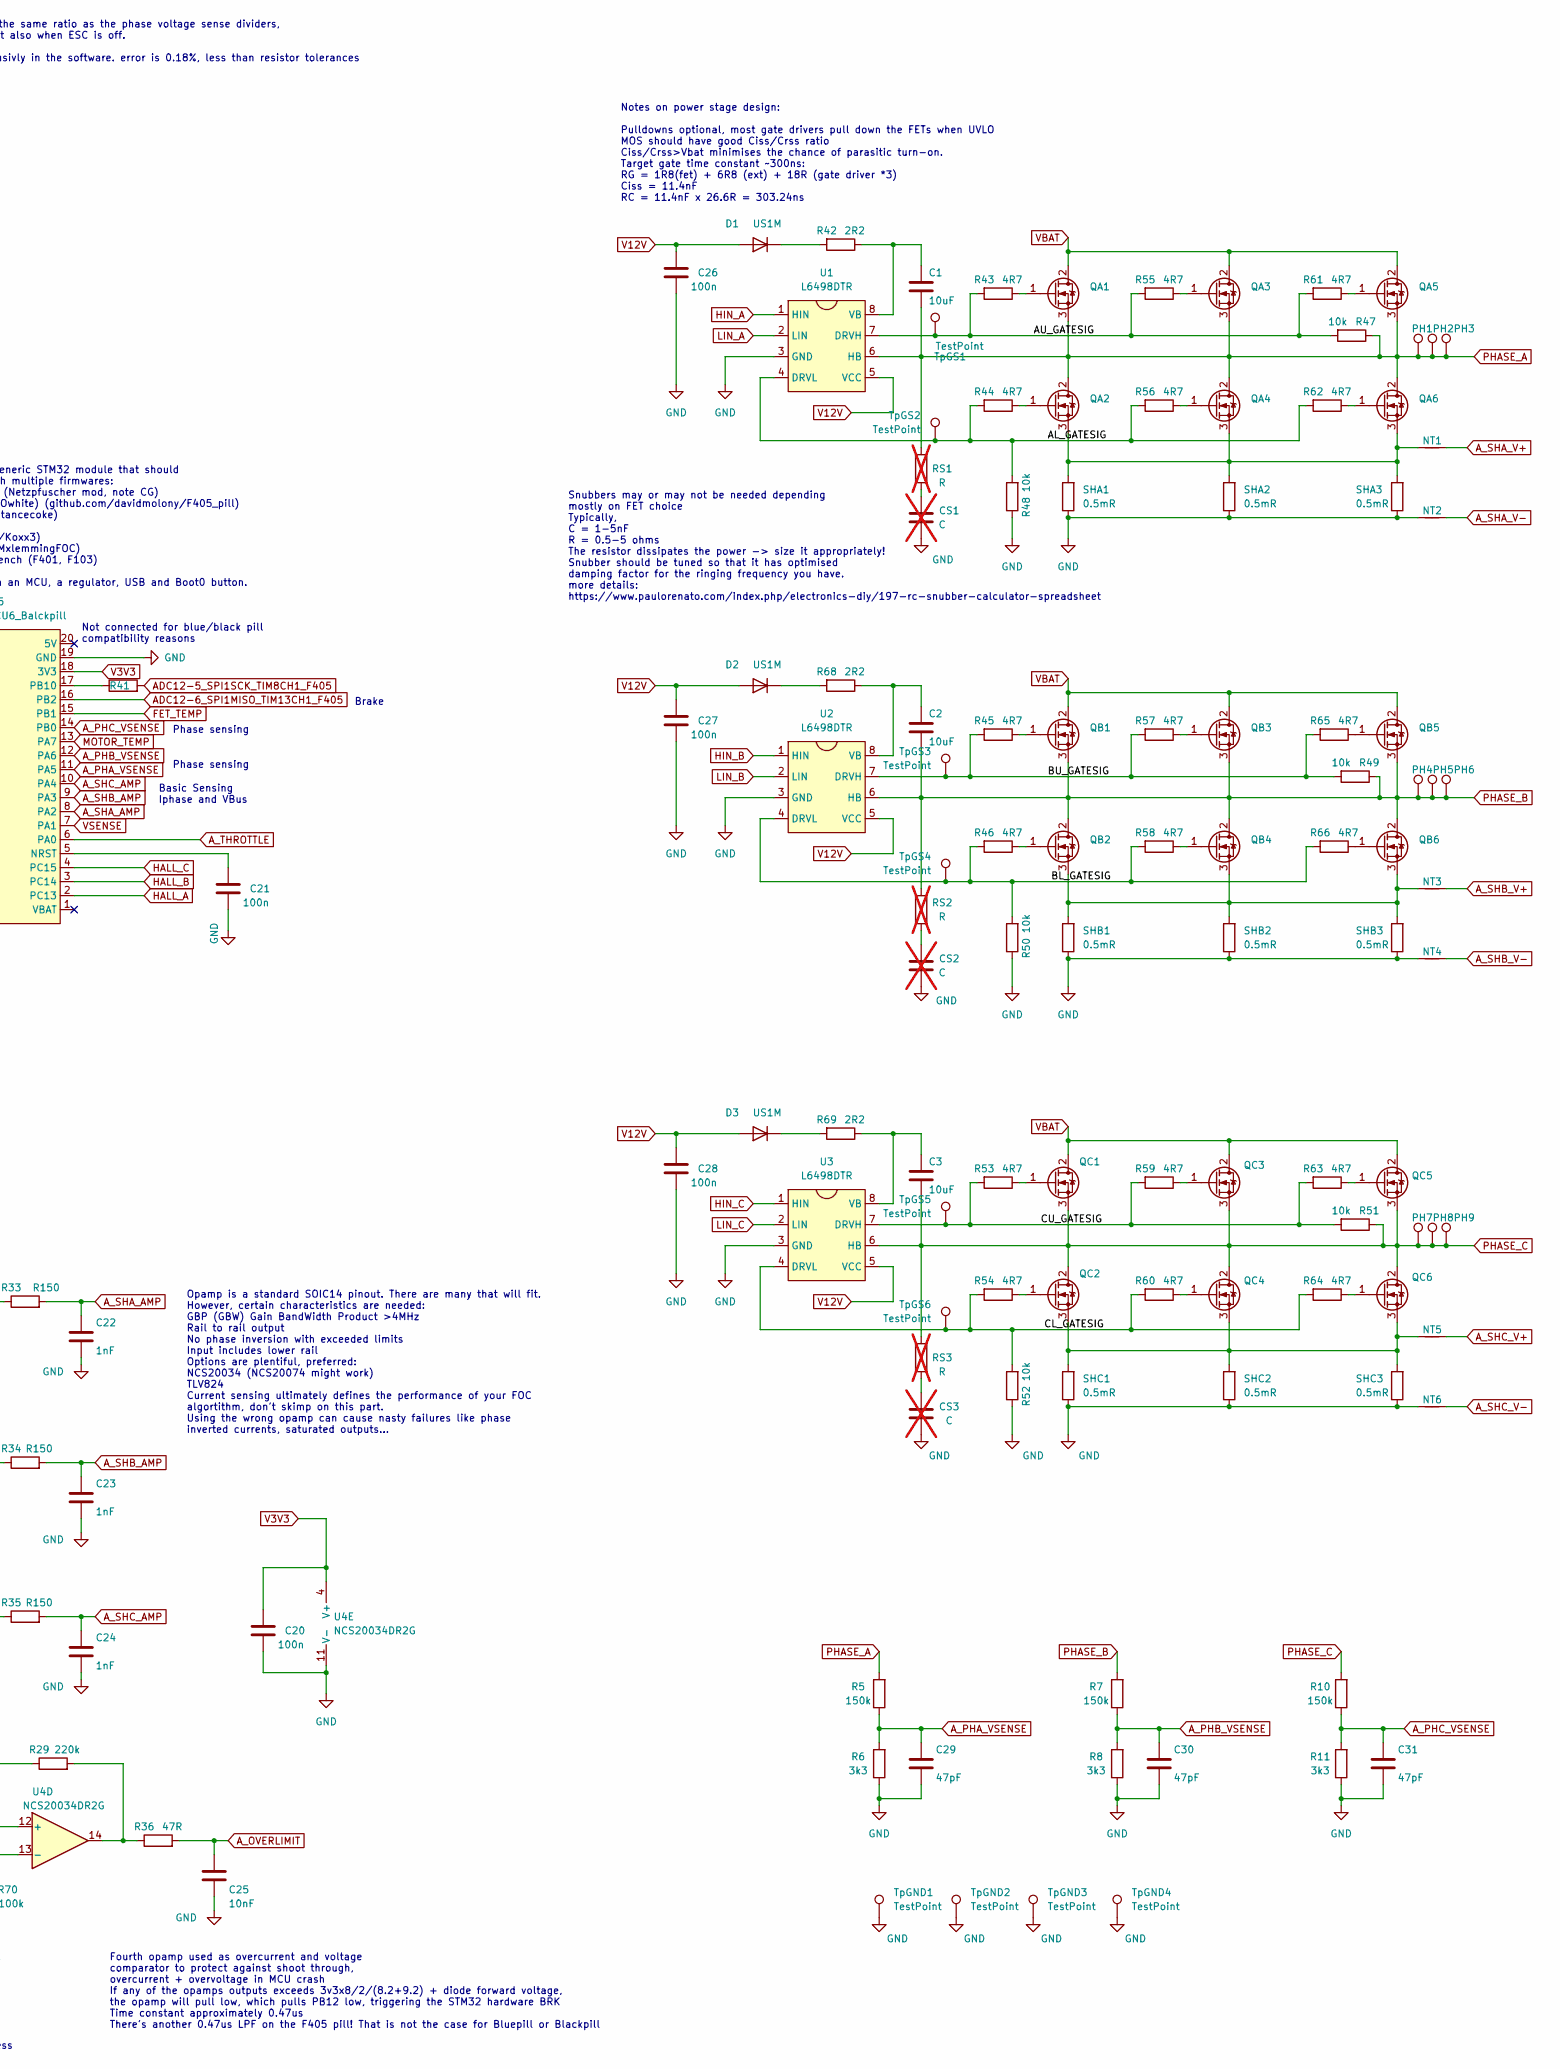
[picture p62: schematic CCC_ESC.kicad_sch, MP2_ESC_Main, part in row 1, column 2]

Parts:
C1, C2, C3, C8, C9, C10, C11, C12, C13: 10uF; C_0603_1608Metric; LCSC C96446
C5: 100nF; C_0805_2012Metric; LCSC C342865
C6, C7, C20, C21, C26, C27, C28: 100n; C_0603_1608Metric; LCSC C14663
C14, C15, C16, C22, C23, C24: 1nF; C_0603_1608Metric; LCSC C1588
C17: 100nF; C_0603_1608Metric; LCSC C14663
C18, C32: 1uF; C_0603_1608Metric; LCSC C15849
C19: 3.3nF; C_0603_1608Metric; LCSC C1613
C25: 10nF; C_0603_1608Metric; LCSC C57112
C29, C30, C31: 47pF; C_0603_1608Metric; LCSC C1671
CS1, CS2, CS3: C; C_0805_2012Metric; not fitted
CX1, CX2, CX3, CX4, CX5, CX6, CX7, CX8: 470uF; CAP_Polaryzed
CX11, CX12, CX13, CX14, CX15, CX16, CX17, CX18, CX19, CX20, CX21, CX22, CX23, CX24, CX25, CX26, CX27, CX28, CX29, CX30, CX31, CX32: 470nF; C_1210_3225Metric; LCSC C192761
D1, D2, D3: US1M; D_SMA; LCSC C412437
D4, D5, D6: D_Small; D_SOD-323; LCSC C191023
D9: LED; D_0603_1608Metric; LCSC C72041
J1: Conn_01x07; JST_PH_B7B-PH-K_1x07_P2.00mm_Vertical
J2, J3, J4: Conn_01x06; JST_PH_B6B-PH-K_1x06_P2.00mm_Vertical
JP1, JP2, JP3: SolderJumper_3_Open; SolderJumper-3_P1.3mm_Open_RoundedPad1.0x1.5mm_NumberLabels
NT1, NT2, NT3, NT4, NT5, NT6: NetTie_2; NetTie-2_SMD_Pad0.5mm
NTC1: Conn_01x02; R_Axial_DIN0204_L3.6mm_D1.6mm_P1.90mm_Vertical; not fitted
PH1, PH2, PH3, PH4, PH5, PH6, PH7, PH8, PH9: PhasePad
QA1, QA2, QA3, QA4, QA5, QA6: CRST030N10N; TO220_horizontal_smallgate
QB1, QB2, QB3, QB4, QB5, QB6: CRST030N10N; TO220_horizontal_smallgate
QC1, QC2, QC3, QC4, QC5, QC6: CRST030N10N; TO220_horizontal_smallgate
R1, R2: 4R7; R_0805_2012Metric; LCSC C17675
R5, R7, R10: 150k; R_0805_2012Metric; LCSC C17470
R6, R8, R11: 3k3; R_0603_1608Metric; LCSC C22978
R9, R28: 1k8; R_0603_1608Metric; LCSC C4177
R12, R27, R47, R48, R49, R50, R51, R52: 10k; R_0603_1608Metric; LCSC C25804
R13, R19, R20, R22, R23, R25, R26: 2k2; R_0603_1608Metric; LCSC C4190
R14: 360k; R_0805_2012Metric; LCSC C17645
R15: 8k2; R_0603_1608Metric; LCSC C25981
R16: 1k; R_0603_1608Metric; LCSC C21190
R17: 22k; R_0603_1608Metric; LCSC C31850
R18, R21, R24, R70: 100k; R_0603_1608Metric; LCSC C25803
R29, R38: 220k; R_0603_1608Metric; LCSC C22961
R30, R31, R32: 47k; R_0603_1608Metric; LCSC C25819
R33, R34, R35: R150; R_0603_1608Metric; LCSC C22808
R36: 47R; R_0603_1608Metric; LCSC C23182
R37, R39, R41: R100; R_0603_1608Metric; LCSC C22775
R42, R68, R69: 2R2; R_0603_1608Metric; LCSC C22939
R43, R44, R45, R46, R53, R54, R56, R57, R58, R59, R60, R61, R62, R63, R64, R65, R66: 4R7; R_0603_1608Metric; LCSC C23164
R55: 4R7; R_0603_1608Metric; LCSC C23214
R67: 30k; R_0603_1608Metric; LCSC C22984
RN1, RN4: 10k; R_Array_Concave_4x0603; LCSC C29718
RN2, RN3, RN5: 470R; R_Array_Concave_4x0603; LCSC C25510
RS1, RS2, RS3: R; R_0805_2012Metric; not fitted
SHA1, SHA2, SHA3: 0.5mR; Shunt_2512_6332Metric; LCSC C349161
SHB1, SHB2, SHB3: 0.5mR; Shunt_2512_6332Metric; LCSC C349161
SHC1, SHC2, SHC3: 0.5mR; Shunt_2512_6332Metric; LCSC C349161
SW1: Conn_01x02; R_1206_3216Metric_Pad1.30x1.75mm_HandSolder; not fitted
Tp12V1: 12V Pad; TestPoint_THTPad_D2.0mm_Drill1.0mm
TpGND1, TpGND2, TpGND3: TestPoint; TestPoint_THTPad_D2.0mm_Drill1.0mm
TpGND4: TestPoint; TestPoint_THTPad_D3.0mm_Drill1.5mm
TpGS1, TpGS2, TpGS3, TpGS4, TpGS5, TpGS6: TestPoint; TestPoint_THTPad_D2.0mm_Drill1.0mm
TpOCP1: TestPoint; TestPoint_THTPad_D2.0mm_Drill1.0mm
U1, U2, U3: L6498DTR; SOIC-8_3.9x4.9mm_P1.27mm; LCSC C500658
U4: NCS20034DR2G; SOIC-14_3.9x8.7mm_P1.27mm; LCSC C695777
U5: STM32F401CCU6_Balckpill; Blackpill_STM32F401CEU6
U6: PQDE6W-Q110 / RD5-110S12W; PQDE6W
U7: TO220_replacement_module

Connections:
/AL_GATESIG: R44.2, R48.2, R56.2, R62.2, TpGS2.1, U1.4 (DRVL)
/AU_GATESIG: R43.2, R47.2, R55.2, R61.2, TpGS1.1, U1.7 (DRVH)
/BL_GATESIG: R46.2, R50.2, R58.2, R66.2, TpGS4.1, U2.4 (DRVL)
/BU_GATESIG: R45.2, R49.2, R57.2, R65.2, TpGS3.1, U2.7 (DRVH)
/CL_GATESIG: R52.2, R54.2, R60.2, R64.2, TpGS6.1, U3.4 (DRVL)
/CU_GATESIG: R51.2, R53.2, R59.2, R63.2, TpGS5.1, U3.7 (DRVH)
ADC12-5_SPI1SCK_TIM8CH1_F405: J1.7, R41.2
ADC12-6_SPI1MISO_TIM13CH1_F405: C32.1, RN5.4 (R4.1), U5.16 (PB2)
A_OVERLIMIT: C25.1, R36.2, U5.21 (PB12)
A_PHA_VSENSE: C29.1, R5.1, R6.2, U5.11 (PA5)
A_PHB_VSENSE: C30.1, R7.1, R8.2, U5.12 (PA6)
A_PHC_VSENSE: C31.1, R10.1, R11.2, U5.14 (PB0)
A_SHA_AMP: C22.1, D6.2 (A), R33.2, U5.8 (PA2)
A_SHA_V+: NT1.2, R19.2
A_SHA_V-: NT2.2, R20.2
A_SHB_AMP: C23.1, D5.2 (A), R34.2, U5.9 (PA3)
A_SHB_V+: NT3.2, R22.2
A_SHB_V-: NT4.2, R23.2
A_SHC_AMP: C24.1, D4.2 (A), R35.2, U5.10 (PA4)
A_SHC_V+: NT5.2, R25.2
A_SHC_V-: NT6.2, R26.2
A_THROTTLE: C18.1, RN5.3 (R3.1), U5.6 (PA0)
FET_TEMP: NTC1.2, R12.1, U5.15 (PB1)
GND: C5.2, C6.2, C7.2, C8.2, C9.2, C10.2, C11.2, C12.2, C13.2, C14.2, C15.2, C16.2, C17.2, C18.2, C19.2, C20.2, C21.2, C22.2, C23.2, C24.2, C25.2, C26.2, C27.2, C28.2, C29.2, C30.2, C31.2, C32.2, CS1.1, CS2.1, CS3.1, CX1.2, CX2.2, CX3.2, CX4.2, CX5.2, CX6.2, CX7.2, CX8.2, CX11.2, CX12.2, CX13.2, CX14.2, CX15.2, CX16.2, CX17.2, CX18.2, CX19.2, CX20.2, CX21.2, CX22.2, CX23.2, CX24.2, CX25.2, CX26.2, CX27.2, CX28.2, CX29.2, CX30.2, CX31.2, CX32.2, J1.2, J2.2, J3.1, J4.2, NT2.1, NT4.1, NT6.1, NTC1.1, R6.1, R8.1, R9.1, R11.1, R15.1, R17.1, R28.2, R38.1, R48.1, R50.1, R52.1, R67.1, R70.2, SHA1.1, SHA2.1, SHA3.1, SHB1.1, SHB2.1, SHB3.1, SHC1.1, SHC2.1, SHC3.1, TpGND1.1, TpGND2.1, TpGND3.1, TpGND4.1, U1.3 (GND), U2.3 (GND), U3.3 (GND), U4.11 (V-), U5.19 (GND), U5.39 (GND), U6.2 (GND_IN), U6.3 (GND_OUT), U7.2 (GND)
HALL_A: C16.1, RN1.1 (R1.1), U5.2 (PC13)
HALL_B: C15.1, RN1.2 (R2.1), U5.3 (PC14)
HALL_C: C14.1, RN1.3 (R3.1), U5.4 (PC15)
HIN_A: U1.1 (HIN), U5.25 (PA8)
HIN_B: U2.1 (HIN), U5.26 (PA9)
HIN_C: U3.1 (HIN), U5.27 (PA10)
LIN_A: U1.2 (LIN), U5.22 (PB13)
LIN_B: U2.2 (LIN), U5.23 (PB14)
LIN_C: U3.2 (LIN), U5.24 (PB15)
MOTOR_TEMP: C17.1, RN1.4 (R4.1), U5.13 (PA7)
unnamed: CS1.2, RS1.1
unnamed: CS2.2, RS2.1
unnamed: CS3.2, RS3.1
unnamed: D1.1 (K), R42.2
unnamed: D2.1 (K), R68.2
unnamed: D3.1 (K), R69.2
unnamed: D9.1 (K), R67.2
unnamed: J1.1, JP2.2 (C)
unnamed: J1.3, RN5.1 (R1.1)
unnamed: J1.4, RN5.2 (R2.1)
unnamed: J2.1, JP1.2 (C)
unnamed: J3.2, RN1.8 (R1.2), RN4.5 (R4.2)
unnamed: J3.3, RN1.7 (R2.2), RN4.6 (R3.2)
unnamed: J3.4, RN1.6 (R3.2), RN4.7 (R2.2)
unnamed: J3.5, RN1.5 (R4.2), RN4.8 (R1.2)
unnamed: J4.1, JP3.2 (C)
unnamed: NT1.1, QA2.3, QA4.3, QA6.3, SHA1.2, SHA2.2, SHA3.2
unnamed: NT3.1, QB2.3, QB4.3, QB6.3, SHB1.2, SHB2.2, SHB3.2
unnamed: NT5.1, QC2.3, QC4.3, QC6.3, SHC1.2, SHC2.2, SHC3.2
unnamed: QA1.1, R43.1
unnamed: QA2.1, R44.1
unnamed: QA3.1, R55.1
unnamed: QA4.1, R56.1
unnamed: QA5.1, R61.1
unnamed: QA6.1, R62.1
unnamed: QB1.1, R45.1
unnamed: QB2.1, R46.1
unnamed: QB3.1, R57.1
unnamed: QB4.1, R58.1
unnamed: QB5.1, R65.1
unnamed: QB6.1, R66.1
unnamed: QC1.1, R53.1
unnamed: QC2.1, R54.1
unnamed: QC3.1, R59.1
unnamed: QC4.1, R60.1
unnamed: QC5.1, R63.1
unnamed: QC6.1, R64.1
unnamed: R16.1, R17.2, R27.2
unnamed: R29.2, R36.1, U4.14
unnamed: R30.2, R33.1, U4.1
unnamed: R31.2, R34.1, U4.7
unnamed: R32.2, R35.1, U4.8
unnamed: RN2.1 (R1.1), U5.33 (PB5)
unnamed: RN2.2 (R2.1), U5.32 (PB4)
unnamed: RN2.3 (R3.1), U5.31 (PB3)
unnamed: RN2.4 (R4.1), U5.30 (PA15)
unnamed: RN3.1 (R1.1), U5.37 (PB9)
unnamed: RN3.2 (R2.1), U5.36 (PB8)
unnamed: RN3.3 (R3.1), U5.35 (PB7)
unnamed: RN3.4 (R4.1), U5.34 (PB6)
unnamed: R28.1, RN5.6 (R3.2), RN5.8 (R1.2)
unnamed: R9.2, RN5.5 (R4.2), RN5.7 (R2.2)
unnamed: C5.1, SW1.1, U6.1 (VIN)
unnamed: R1.1, R2.1, SW1.2
unnamed: C1.1, R42.1, U1.8 (VB)
unnamed: C2.1, R68.1, U2.8 (VB)
unnamed: C3.1, R69.1, U3.8 (VB)
unnamed: R18.1, R19.1, U4.3 (+)
unnamed: R20.1, R30.1, U4.2 (-)
unnamed: R21.1, R22.1, U4.5 (+)
unnamed: R23.1, R31.1, U4.6 (-)
unnamed: R24.1, R25.1, U4.10 (+)
unnamed: R26.1, R32.1, U4.9 (-)
unnamed: R27.1, R29.1, U4.12 (+)
unnamed: C21.1, U5.5 (NRST)
unnamed: R37.2, U5.28 (PA11)
unnamed: R39.2, U5.29 (PA12)
unnamed: R41.1, U5.17 (PB10)
OVERCURRENT: D4.1 (K), D5.1 (K), D6.1 (K), R70.1, TpOCP1.1, U4.13 (-)
PA15 TIM2 CH1: J4.6, RN2.5 (R4.2)
PB3 SCK TIM2CH2: J4.5, RN2.6 (R3.2)
PB4 MISO TIM3 CH1: J4.4, R13.1, RN2.7 (R2.2)
PB5 MOSI TIM3 CH2: J4.3, R13.2, RN2.8 (R1.2)
PB6 D_UART1_TX I2C1_SCL TIM4_CH1: J2.6, RN3.5 (R4.2)
PB7 D_UART1_RX I2C1_SDA TIM4_CH2: J2.5, RN3.6 (R3.2)
PB8 DI2C1_SCL TIM4_CH3: J2.4, RN3.7 (R2.2)
PB9 DI2C1_SDA TIM4_CH4: J2.3, RN3.8 (R1.2)
PHASE_A: C1.2, PH1.1, PH2.1, PH3.1, QA1.3, QA2.2, QA3.3, QA4.2, QA5.3, QA6.2, R5.2, R47.1, RS1.2, U1.6 (HB)
PHASE_B: C2.2, PH4.1, PH5.1, PH6.1, QB1.3, QB2.2, QB3.3, QB4.2, QB5.3, QB6.2, R7.2, R49.1, RS2.2, U2.6 (HB)
PHASE_C: C3.2, PH7.1, PH8.1, PH9.1, QC1.3, QC2.2, QC3.3, QC4.2, QC5.3, QC6.2, R10.2, R51.1, RS3.2, U3.6 (HB)
UART3RX_I2C2SDA_ADC12-15_F405: J1.5, R39.1
UART3TX_I2C2SCL_ADC12-14_F405: J1.6, R37.1
V3V3: C6.1, C7.1, C20.1, JP1.3 (B), JP2.3 (B), JP3.3 (B), R12.2, R16.2, R18.2, R21.2, R24.2, RN4.1 (R1.1), RN4.2 (R2.1), RN4.3 (R3.1), RN4.4 (R4.1), U4.4 (V+), U5.18 (3V3), U5.40 (3V3)
V5V: C8.1, C9.1, C10.1, D9.2 (A), J3.6, JP1.1 (A), JP2.1 (A), JP3.1 (A), U5.38 (5V), U7.3 (VOUT)
V12V: C11.1, C12.1, C13.1, C26.1, C27.1, C28.1, D1.2 (A), D2.2 (A), D3.2 (A), Tp12V1.1, U1.5 (VCC), U2.5 (VCC), U3.5 (VCC), U6.4 (VOUT), U7.1 (VIN)
VBAT: CX1.1, CX2.1, CX3.1, CX4.1, CX5.1, CX6.1, CX7.1, CX8.1, CX11.1, CX12.1, CX13.1, CX14.1, CX15.1, CX16.1, CX17.1, CX18.1, CX19.1, CX20.1, CX21.1, CX22.1, CX23.1, CX24.1, CX25.1, CX26.1, CX27.1, CX28.1, CX29.1, CX30.1, CX31.1, CX32.1, QA1.2, QA3.2, QA5.2, QB1.2, QB3.2, QB5.2, QC1.2, QC3.2, QC5.2, R1.2, R2.2, R14.2
VSENSE: C19.1, R14.1, R15.2, R38.2, U5.7 (PA1)

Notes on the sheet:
R4, R15 and R38 were chosen to have exactly the same ratio as the phase voltage sense dividers, but significatnly less current. since they are hot also when ESC is off. So you can use the 3.3k and 150k values exclusivly in the software. error is 0.18%, less than resistor tolerances
for electrolytic cap: user LOW ESR caps. most 160V electrolytic caps have absolutely atrocious ESR (greather than 1R!) ideal range - 220-470 uF.
The "Pill" is chosen as a generic STM32 module that should allow easy compatibility with multiple firmwares: VESC with GD32F303CG pill (Netzpfuscher mod, note CG) VESC with STM32F405 pill (Owhite) (github.com/davidmolony/F405_pill) EBICS with F103 Bluepill (Stancecoke) SmartESC V3 (Casainho) SmartE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
Likely use case: PWM Throttle Incremental Encoder Screen Comms Peripherals GPIO
DO NOT CONNECT on blue/black pill
20...47uF cap is used which together with R1 and R2 creates a sort of LPF protecting the DCDC from high frequency noise/spikes.
Hall sensor filter at ~16kHz
Likely use case: PWM Throttle Encoder on SPI, SSI or Incremental Peripherals GPIO
Not connected for blue/black pill compatibility reasons
Reserved over limits protection
DCDC modules widely available as drop in replacement for TO-220 regulators
Fourth opamp used as overcurrent and voltage comparator to protect against shoot through, overcurrent + overvoltage in MCU crash If any of the opamps outputs exceeds 3v3x8/2/(8.2+9.2) + diode forward voltage, the opamp will pull low, which pulls PB12 low, triggering the STM32 hardware BRK Time cons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
Snubbers may or may not be needed depending mostly on FET choice Typically, C = 1-5nF R = 0.5-5 ohms The resistor dissipates the power -> size it appropriately! Snubber should be tuned so that it has optimised damping factor for the ringing frequency you have. more details: https://www.paulorenato.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
Input impedance 100R on every pin makes it much more resilient to ESD, cross wiring, GPIO-GND/3V3 etc
Opamp is a standard SOIC14 pinout. There are many that will fit. However, certain characteristics are needed: GBP (GBW) Gain BandWidth Product >4MHz Rail to rail output No phase inversion with exceeded limits Input includes lower rail Options are plentiful, preferred: NCS20034 (NCS20074 might work)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
options for ceramic decoupling cap: 200V: NM1206B474K201CEGN / C725802 - 1206 250V: FM32X684K251EGG / C692307 - 1210
Notes on power stage design: Pulldowns optional, most gate drivers pull down the FETs when UVLO MOS should have good Ciss/Crss ratio Ciss/Crss>Vbat minimises the chance of parasitic turn-on. Target gate time constant ~300ns: RG = 1R8(fet) + 6R8 (ext) + 18R (gate driver *3) Ciss = 11.4nF RC = 11.4nF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
Phase sensing
MISO and MOSI are useful to have a link in case of one wire SSI DNP if full duplex required
Brake
Use low forward voltage diodes 1N5817 or 1N5819 is a good choice Forward voltage at 1mA >0.3V will render this useless
Reserved PWM
Basic Sensing Iphase and VBus
Footprint for CUI isolated module for up to 160V operation. Only allows 500mA. HiLink HLK-10D11012 CUI PQDE6W-Q110 Or anything that exceeds your battery voltage and gives 12V out

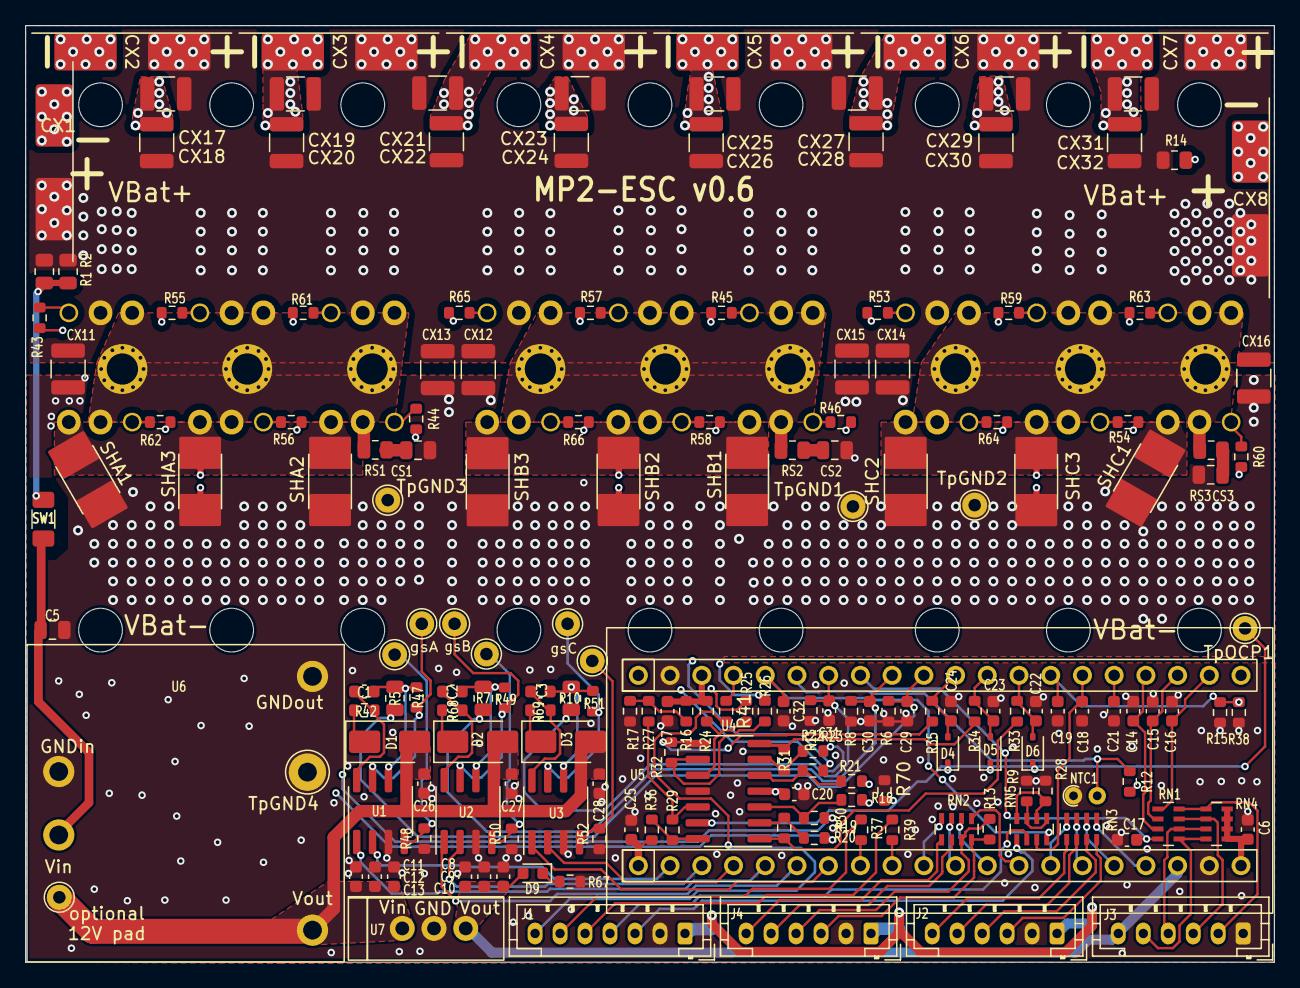
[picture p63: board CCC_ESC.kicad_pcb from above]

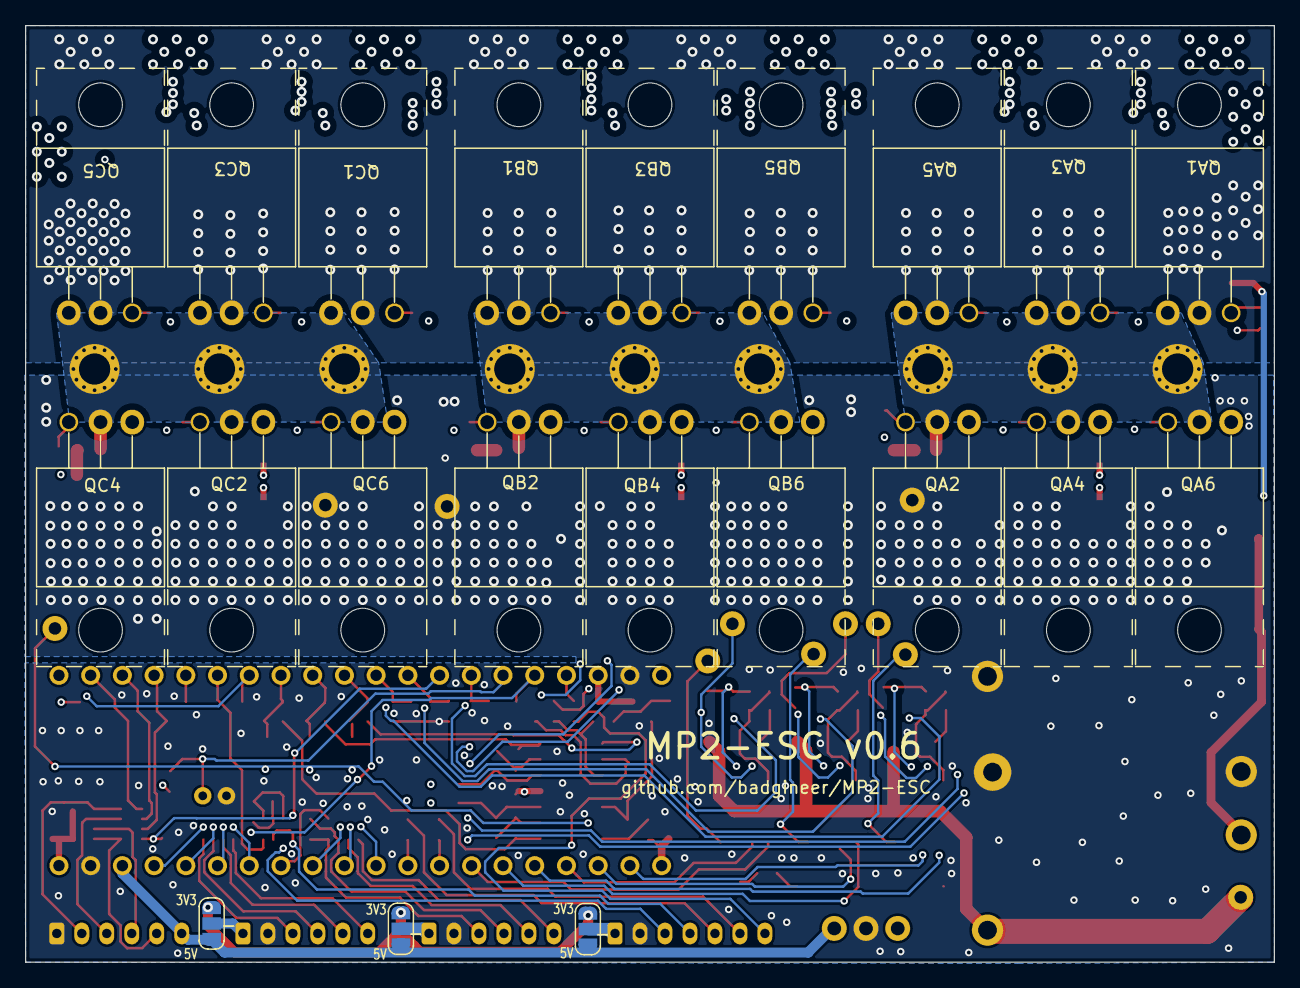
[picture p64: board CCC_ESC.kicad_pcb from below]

Board: 4 copper layers, 100.0 x 75.0 mm, 216 parts (21 on the bottom side), 121 nets.

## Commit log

2022-05-18 initial commit, schematic in work, nothing else
    [CCC_ESC.kicad_pcb, CCC_ESC.kicad_sch, io.kicad_sch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]
2022-05-21 Tidy up some things, add hardware overcurrent protection, implement the phase sensors, add input impedances and suggested use cases,
    [CCC_ESC.kicad_pcb, CCC_ESC.kicad_sch]
2022-05-30 schematic updates, part updates
    [CCC_ESC.kicad_sch]
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2022-06-03 Route it. Nearly finished...
    [CCC_ESC.kicad_pcb, CCC_ESC.kicad_sch]
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2022-06-13 work in progress - added some values and part numbers
    [CCC_ESC.kicad_sch]
2022-06-18 work in progress - pcb work all parts are on the board again
    [CCC_ESC.kicad_pcb]
2022-06-18 work in progress - pcb work tiny change
    [CCC_ESC.kicad_pcb]
2022-06-18 work in progress - some schematic updates, some minor routing
    [CCC_ESC.kicad_pcb, CCC_ESC.kicad_sch]
2022-06-19 added cap and JST
    [CCC_ESC.kicad_pcb, CCC_ESC.kicad_sch]
2022-06-20 gate drivers PCB change and other minor stuff
    [CCC_ESC.kicad_pcb, CCC_ESC.kicad_sch]
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2022-06-20 minor schematic + routing optimisation
    [CCC_ESC.kicad_pcb, CCC_ESC.kicad_sch]
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2022-06-21 finished most routing except gate signals
    [CCC_ESC.kicad_pcb]
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2022-06-23 routed phase sense signal wires and some power
    [CCC_ESC.kicad_pcb]
2022-06-23 power planes, some finihes
    [CCC_ESC.kicad_pcb]
2022-06-24 new footprint for electrolytic caps so we avoid the fet body
    [CCC_ESC.kicad_sch]
2022-06-24 finished power and gnd planes and pours
    [CCC_ESC.kicad_pcb, CCC_ESC.kicad_sch]
2022-06-24 improved nettie gnd to not touch other gnds
    [CCC_ESC.kicad_pcb]
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2022-06-25 second dcdc footprint and improved to220 replacement footprint
    [CCC_ESC.kicad_pcb, CCC_ESC.kicad_sch]
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2022-07-01 grotesque spectacle of microoptimisations - continued
    [CCC_ESC.kicad_pcb]
2022-07-01 hope you like vias
    [CCC_ESC.kicad_pcb]
2022-07-03 so you don't like vias
    [CCC_ESC.kicad_pcb, CCC_ESC.kicad_sch]
2022-07-03 redid vias on phase areas
    [CCC_ESC.kicad_pcb]
2022-07-04 redid vias on vbus and cap pads
    [CCC_ESC.kicad_pcb]
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2022-07-04 rearranged opamp adiacent SMDs
    [CCC_ESC.kicad_pcb]
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2022-07-04 some extra gnd vias
    [CCC_ESC.kicad_pcb]
2022-07-04 moved last vias out of pads
    [CCC_ESC.kicad_pcb]
2022-07-06 branding! .... and some vias
    [CCC_ESC.kicad_pcb]
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2022-07-06 cant stop moving vias around!
    [CCC_ESC.kicad_pcb]
2022-07-06 Add testpoints, change capacitor footprints, clean up labels, add extra switch node plane, add extra DCDC ground (TP)
    [CCC_ESC.kicad_pcb, CCC_ESC.kicad_sch]
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2022-07-11 started phase node redesign. a mess at the moment
    [CCC_ESC.kicad_pcb]
2022-07-14 phase nodes redesigned
    [CCC_ESC.kicad_pcb]
2022-07-14 moved some traces to inner2, not all yet
    [CCC_ESC.kicad_pcb]
2022-07-15 moved current sense to inner2, changed nettie topology
    [CCC_ESC.kicad_pcb]
2022-07-16 Modify spacing on MOSFETs to put groups closer and phases further apart Change pinout on hall sensors
    [CCC_ESC.kicad_pcb, CCC_ESC.kicad_sch]
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2022-07-18 Few BoM fixes, add notes on snubbers, opamp, dcdc, MOSFET choices
    [CCC_ESC.kicad_sch]
2022-07-18 labels for solderjumpers, some minor adjustments
    [CCC_ESC.kicad_pcb, CCC_ESC.kicad_sch]
2022-07-18 imported changes from schematic, parity warnings disappeared from DRC
    [CCC_ESC.kicad_pcb]
2022-07-20 microoptimisations in area of resistor values
    [CCC_ESC.csv, CCC_ESC.kicad_sch]
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2022-07-22 widened the board with 7mm and increased the GNDbus bar space with 3mm
    [CCC_ESC.kicad_pcb]
2022-07-24 added a lot of gnd bus bar vias
    [CCC_ESC.kicad_pcb]
2022-07-24 added vbus vias and widened the vbus bus bar space
    [CCC_ESC.kicad_pcb]
2022-07-24 moved a decoupling mlcc to a low impedance place/trace
    [CCC_ESC.kicad_pcb]
2022-07-24 added some missing vbus vias
    [CCC_ESC.kicad_pcb]
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2022-07-25 Tidy up some errant positions, few BoM fixes
    [CCC_ESC.kicad_pcb, CCC_ESC.kicad_sch]
2022-07-25 Pre ordering, minor fixes to positions
    [CCC_ESC.csv, CCC_ESC.kicad_pcb, CCC_ESC.kicad_sch]
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2022-08-08 pretty GND bus bar vias
    [CCC_ESC.kicad_pcb]
2022-08-09 many things prettified and minor improvement
    [CCC_ESC.kicad_pcb, CCC_ESC.kicad_sch]
2022-08-11 changed cap to TVS. prettyfied some stuff.
    [CCC_ESC.kicad_pcb, CCC_ESC.kicad_sch]
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2022-09-05 bigger shunt pads, some minor trace adjustments in inner2
    [CCC_ESC.kicad_pcb, CCC_ESC.kicad_sch]
2022-09-06 fixed minor bugs, added gnd vias
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2022-09-16 moved to 0.5mohm shunts, minor shunt orientation improvement
    [CCC_ESC.kicad_sch]
2022-09-20 deleted snubboer part number. snubber depends on fet
    [CCC_ESC.kicad_sch]
2022-10-02 changed voltage dividers, added vbat pads, some other minor stuff
    [CCC_ESC.kicad_sch]
2022-10-17 changed shunts to one available on jlcpcb for assembly
    [CCC_ESC.kicad_sch]
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2022-10-28 solder jumpers for vsense and overvoltage protection now on pcb
    [CCC_ESC.kicad_sch]
2022-10-28 fixed R1 and R2 values. Thanks, Owen! Also regenerated Fabriaction files
    [CCC_ESC-B_Cu.gbr, CCC_ESC-B_Mask.gbr, CCC_ESC-B_Paste.gbr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]
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2022-11-06 low loss diodes, some layout enhancemets, some extra lines in the docu
    [CCC_ESC.kicad_sch]
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2022-11-08 many tiny layout tweaks, new extra footprint for big TVS on back for hand soldering
    [CCC_ESC.kicad_sch]
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2023-01-28 changed values for RC LPF of overlimit Opamp
    [CCC_ESC.kicad_sch]
2023-01-28 moved cap near PB12 for better on-pcb properties
    [CCC_ESC.kicad_sch]
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2023-01-29 redesigned the grenade safety pin / fuse area
    [CCC_ESC.kicad_sch]
2023-01-29 redesign and increase margins from HV traces to 0.4mm
    [CCC_ESC.kicad_sch]
2023-02-01 increased clearance for HV traces to 0.5mm
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2023-02-14 WIP - creating space. ALL IS BROKEN ATM
    [CCC_ESC.kicad_sch]
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2023-02-26 optimised via stitching for batttery pads on the right
    [CCC_ESC.kicad_sch]
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2023-03-02 added 2 1uF caps on throttle input to smooth out throttle signal
    [CCC_ESC.kicad_sch]
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2023-03-11 docs, moved to kicad 7, some minor kicad 7 related fixes
    [CCC_ESC.kicad_sch]
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2023-07-25 added bootstrap resistors to limit huge current spike through diode.
    [CCC_ESC.kicad_sch]
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2023-09-01 switched to better gate drivers, reduced gate pulldowns to 10k, fixed bug
    [CCC_ESC.kicad_sch]
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2023-10-27 Simplified 150v setup (#18)
    * vsense2 cleanup, opamp pulldown
    * changed vbat divider and overvoltage opamp resistor
    * chaed capacitors to 200+ v, deleted TVSs
    * fiexed a few resistor values I broke
    * minor adjustments
    * fixed 2 bugs, changed shunt part number, since the old one is out of stock
    * added gate charge calculator spreadsheet
    * fixed gate resistor calculation spreadsheet
    * Update README.md
    * Update README.md
    [CCC_ESC.kicad_pcb, CCC_ESC.kicad_sch, Gate_resistor_calculator_MP2.ods]
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2023-11-26 vphase sensse now actually to 150 like it should jhave been
    [CCC_ESC.kicad_pcb, CCC_ESC.kicad_sch]
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
